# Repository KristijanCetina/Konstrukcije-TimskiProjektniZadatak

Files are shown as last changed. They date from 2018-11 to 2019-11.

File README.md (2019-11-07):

# Konstrukcije - Timski projektni zadatak
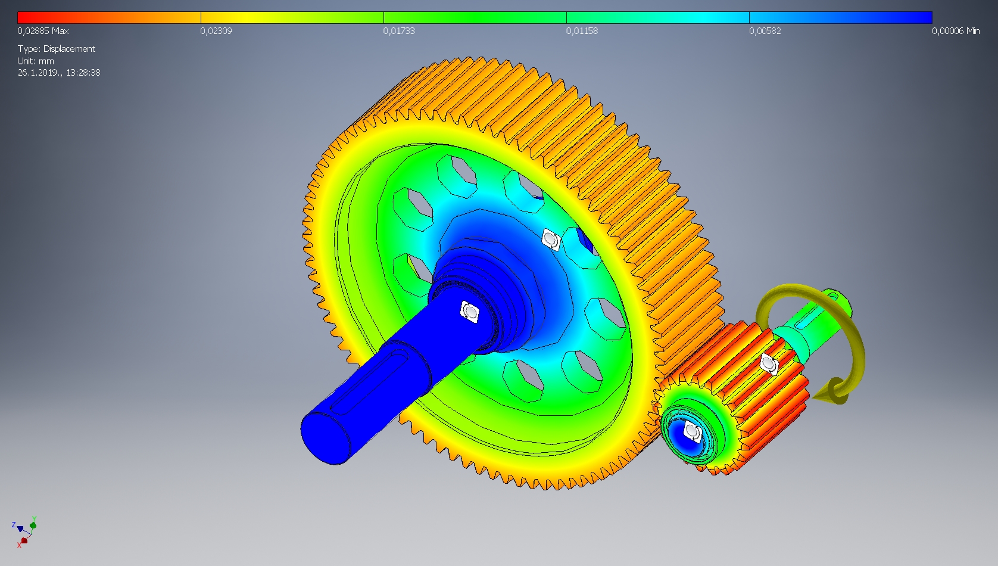
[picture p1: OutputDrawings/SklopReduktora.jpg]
Sklop reduktora Sklop Reduktora

U ovom radu predstavljamo proračun strojnog sklopa - 1-stupanjskog reduktora zajedno s pripradajućim vratilima i ležajevima koji je zadan kao timski projektni zadatak iz kolegija Konstrukcije.

Projektni zadatak se sastoji od proračuna zupčanika, vratila i ležajeva sukladno [zadanim parametrima](https://github.com/KristijanCetina/Konstrukcije-TimskiProjektniZadatak/blob/master/TimskiProjektniZadatak.pdf).

3D model reduktora izrađen je uz pomoć [Autodesk Inventora](https://www.google.com/search?q=Autodesk+Inventor).

Detaljni tok proračuna je izrađen u [LaTeX](https://lmgtfy.com/?q=LaTeX&pp=1&s=g&t=w) te kompajliran u .pdf dokument.  
[PDF verzija proračuna s nacrtom](https://github.com/KristijanCetina/Konstrukcije-TimskiProjektniZadatak/blob/master/Projektni%20zadatak_Cetina-Grgin-Mrkic.pdf)

Sve probleme i greške na koje naiđete slobodno ih prijavite na [Issues tabu](https://github.com/KristijanCetina/Konstrukcije-TimskiProjektniZadatak/issues).

## Uvedena su sljedeća pojednostavljena i zanemareni sljedeći dijelovi proračuna:

* kontrolni proračun
* izbor ulja za podmazivanje
* toplinski proračun
* određivanje stupnja korisnosti

Kod proračuna dimenzija zupčanika zanemareni su sljedeći proračuni:
* nosivost boka zuba
* sigurnost na _pitting_ (površinski zamor)
* nosivost korjena zuba

Kod proračuna vratila izrađena je samo kontrola na plastičnu deformaciju prema normi *DIN 743* te je zanemarena kontrola na zamor materijala.

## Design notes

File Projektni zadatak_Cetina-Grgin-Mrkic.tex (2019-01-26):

\documentclass[11pt,a4paper]{report}
\usepackage[utf8]{inputenc}
\usepackage[croatian]{babel}
\usepackage{amsmath, amsfonts, amssymb}
\usepackage{graphicx}
\usepackage{fancyhdr}
\usepackage{color}
\usepackage {tikz}
\usepackage{pgfplots}
\usetikzlibrary {positioning}
\usepackage{tocloft}
\usepackage[hidelinks]{hyperref}
\usepackage[section]{placeins}
\usepackage[final]{pdfpages}
\bibliographystyle{abbrv}%ieeetr, abbrv
\renewcommand{\cftsecleader}{\cftdotfill{\cftdotsep}}
\addto{\captionscroatian}{\renewcommand{\bibname}{Literatura}}

\usepackage[blocks]{authblk}% The option is for block layout

\newcommand{\kolegij}{}
\newcommand{\naslovRada}{Proračun i konstrukcija 1-stupnjskog reduktora s cilindričnim ravnim zubima \\ {\large Timski projektni zadatak}} 
\newcommand{\mailFriendlynaslovRada}{Konstrukcije - projektni zadatak}

%\author{
%Kristijan Cetina \\{\small JMBAG: 2424011721} \\ {\href{mailto:kcetina@politehnika-pula.hr?subject=\mailFriendlynaslovRada}{{\footnotesize kcetina@politehnika-pula.hr}}} \and 
%Stjepan Grgin \\{\small JMBAG: 0112005802} \\ {\href{mailto:sgrgin@politehnika-pula.hr?subject=\mailFriendlynaslovRada}{{\footnotesize sgrgin@politehnika-pula.hr}}} \and 
%Igor Mrkić \\{\small JMBAG: 0114017089} \\ {\href{mailto:imrkic@politehnika-pula.hr?subject=\mailFriendlynaslovRada}{{\footnotesize imrkic@politehnika-pula.hr}}}
%}

\author[1]{Kristijan Cetina}
\author[2]{Stjepan Grgin}
\author[3]{Igor Mrkić}

\affil[1]{\href{mailto:kcetina@politehnika-pula.hr?subject=\mailFriendlynaslovRada}{kcetina@politehnika-pula.hr} JMBAG: 2424011721}
\affil[2]{\href{mailto:sgrgin@politehnika-pula.hr?subject=\mailFriendlynaslovRada}{sgrgin@politehnika-pula.hr} JMBAG: 0112005802}
\affil[3]{\href{mailto:imrkic@politehnika-pula.hr?subject=\mailFriendlynaslovRada}{imrkic@politehnika-pula.hr} JMBAG: 0114017089}

%\title{\kolegij \\ \naslovRada}
\title{\naslovRada}
\date{Pula, \today}

\begin{document}
\pgfplotsset{width=\textwidth,compat=newest}

\begin{titlepage}
\clearpage
\begin{center}
\begin{Huge}
POLITEHNIKA PULA\\
\end{Huge}
\begin{LARGE}
Visoka tehničko-poslovna škola s p.j.\\
Stručni studij politehnike\\
\end{LARGE}
\end{center}
\vspace{3cm}
{\let\newpage\relax\maketitle}
\thispagestyle{empty}
\vfill
\begin{abstract}

U ovom radu predstavljamo proračun strojnog sklopa 1-stupanjskog reduktora zajedno s pripradajućim vratilima i ležajevima koji je zadan kao sastavni dio kolegija Konstrukcije.

Konstrukcijski sklop izrađen je unutar ograničenja zadanih projektnim zadatkom.
Izrađeni su proračuni dimenzija zopčanika i vratila, proračun momenata i sila na zupčanicima, preliminarni i kontrolni proračun vratila, proračun steznog spoja te valjnih ležajeva.
Na kraju se nalaze radionički nacrti kao i sklopni crtež sklopa.

Elementi proračuna koji su izostavljeni navedeni su u opis zadatka i oganičenja u poglavlju \ref{OpisIOgranicenja}

\vspace{3cm}

\begin{tabbing}
\hspace{50pt}\=\kill
 Kolegij: \> Konstrukcije\\
 Mentori: \> Milenko Jokić, dipl. ing. stroj. \\ 
  \> Feđa Balić, mag. ing. mech.
\end{tabbing} 

\end{abstract}
\end{titlepage}
\includepdf[fitpaper]{TimskiProjektniZadatak.pdf}
\tableofcontents
%\listoftables	%ako ih ima puno prebaci na kraj dokumenta
%\listoffigures	%ako ih ima puno prebaci na kraj dokumenta

%Ovdje kreće rad ili može se koristiti
%\input{filename} (da nastavi pisati kako da je copy/paste) ili
%\include{filename} (da ubaci na novu stranicu. Ok za nova poglavlja i sl)
\chapter{Opis zadatka i ograničenja}\label{OpisIOgranicenja}
\section{Uvod}
Ovaj projektni zadatak nastao je kao obavezni zadatak u sklopu kolegija Konstrukcije koji se održava pod vodstvom Milenka Jokića, dipl.ing., predavača na stručnom studiju politehnike pri Politehnici Pula te asistenciju Feđe Balića, mag. ing. mech.

Prema zadanom predlošku (predložak 3) i zadanim podacima konstriran je 1-stupanjski reduktor s cilindričnim ravnim zubima.
Uvedena su sljedeća pojednostavljena i zanemareni sljedeći dijelovi proračuna:
\begin{itemize}
\item kontrolni proračun
\item izbor ulja za podmazivanje
\item toplinski proračun
\item određivanje stupnja korisnosti
\end{itemize}
Kod proračuna dimenzija zupčanika zanemareni su sljedeći proračuni:
\begin{itemize}
\item nosivost boka zuba
\item sigurnost na \textit{pitting} (površinski zamor)
\item nosivost korjena zuba
\end{itemize}
Kod proračuna vratila izražena je samo kontrola na plastičnu deformaciju te je zanemarena kontrola na zamor materijala.
\newpage
\section{Mehaničke karakteristike materijala}
Zadani materijal za izradu reduktora je Č0745 (E360) čije su karakteristike preuzete iz literature \cite{potrebniMaterijali} te su navedeni u tablici \ref{MehanickeKarakteristikeMaterijala}
\begin{table}[h]
\begin{tabular}{|l|r|}\hline 
Karakteristika & Čvrstoća $\dfrac{N}{mm^2}$ \\ \hline 
Vlačna čvrstoća & $R_m=700 $ \\ \hline 
Granica tečenja & $R_e=370 $ \\ \hline 
Trajna ishodišna dinamička čvrstoča pri vlaku & $R_{d0}=370 $ \\ \hline 
Trajna iizmjenična dinamička čvrstoča pri vlaku/tlaku & $R_{d-1}=320 $ \\ \hline 
Trajna ishodišna dinamička čvrstoča pri savijanju & $R_{ds0}=520 $ \\ \hline 
Trajna izmjenična dinamička čvrstoča pri savijanju & $R_{ds-1}=340 $ \\ \hline 
Trajna ishodišna dinamička čvrstoča pri torziji & $R_{dt0}=260 $ \\ \hline 
Trajna izmjenična dinamička čvrstoča pri torziji & $R_{dt-1}=370 $ \\ \hline 
Granica tečenja pri vlaku/tlaku & $R_{eN}=360 $ \\ \hline 
Granica tečenja pri savijanju & $R_{esN}=430 $ \\ \hline 
Granica tečenja pri torziji & $R_{etN}=250 $ \\ \hline 
\end{tabular} 
Vrijednosti označene s indeksom \emph{N} odnose se na nazivni promjer $d_N=16\,mm$.
\caption{Mehaničke karakteristike korištenog materijala Č0745} \label{MehanickeKarakteristikeMaterijala}
\end{table}

\chapter{Proračun sklopa}
\section{Proračun dimenzija zupčanika}
Na temelju poznatih pogonskih podatak određen je minimalni diobeni promjer pogonskog zupčanika po izrazu
\begin{equation}
d_1\geq 4045 \cdot \sqrt[3]{\frac{P_1}{\psi_b \cdot n_1} \cdot \frac{i_z +1}{i_z}\cdot K_A \cdot 
K_V \cdot K_{H\alpha} \cdot K_{H\beta} \cdot \left(\frac{S_{Hmin}}{\sigma_{Hlim}}\right)^2 }\label{equ:d1minimalno}
\end{equation}
Pri čemu je $\psi_b=1$ - omjer širine zupčanika i diobenog promjera,
$P_1 \, [kW]$ - snaga pogonskog stroja,
$n_1 \, [s^{-1}]$ - broj okretaja pogonskog stroja,
$i_z$ - željeni prijenosni omjer,
$K_A=2$ - faktor primjene očitan iz tablice \cite{potrebniMaterijali},
$K_V=1$ - faktor dodatnih dinamičkih opterećenja,
$K_{H\alpha}=1$ - faktor raspodjele opterećenja na zube koji su istovremeno u zahvatu,
$K_{H\beta}=1$ - faktor raspodjele opterećenja uzduž boka zuba,
$S_{Hmin}=1,3$ - stupanj sigurnosti na površinski zamor (\textit{pitting}),
$\sigma_{H\lim}=1$ - trajna dinamička čvrstoća boka zuba na kontaktna naprezanja.

Uvrštavanje poznatih podataka u \eqref{equ:d1minimalno} dobije se minimalni diobeni promjer pogonskog zupčanika $$d_1\geq 100,3\,mm$$

Broj zuba pogonskog zupčanika određen je u odnosu na njegovu kutnu brzinu po izrazu
\begin{equation}
\nu=\frac{d_1 \cdot n_1 \cdot \pi}{60}\label{equ:kutnaBrzina}
\end{equation}
Uvrštavanje poznatih podataka u \eqref{equ:kutnaBrzina} dobivena je kutna brzina
$$\nu=5,77 ms^{-1}$$
te je iz tablice \cite{potrebniMaterijali} očitan mogući raspon broja zuba te je usvojen 
$$\mathbf{z_1=21}$$
Broj zuba gonjenog zupčanika je određen
\begin{align*}
z_2&=z_1 \cdot i_z\\
z_2&=21 \cdot 4\\
z_2&=\mathbf{84}
\end{align*}
Stvarni i željeni prijenosni omjer su isti $$i_z=\mathbf{i_{stv}=\frac{z_2}{z_1}=4}$$
Normalni modul zuba $m_n$ je izračunat i odabran na osnovu standardnih mjera:
\begin{align*}
m_n&=\frac{d_1}{z_1}\\
m_n&=\frac{100,3}{21}\\
m_n&=4,776 mm \Rightarrow \mathbf{m_n=5\, mm}
\end{align*}
Razmak između osi zupčanika $a$ je određen:
\begin{align*}
a&=\frac{m_n}{2} \cdot (z_1 + z_2)\\
a&=\frac{5}{2} \cdot 105\\
a&=\mathbf{262,5\,mm}
\end{align*}
Stvarni diobeni promjer pogonskog zupčanika izračunat je u odnosu na normalni modul i ranije određen broj zuba
\begin{align*}
d_1&=m_n \cdot z_1\\
d_1&=5 \cdot 21\\
d_1&=\mathbf{105 \, mm}
\end{align*}
Širina gonjenog zupčanika:
\begin{align*}
b_2&=\psi_b \cdot d_1\\
b_2&=1 \cdot 105\\
b_2&=\mathbf{105 \,mm}
\end{align*}
Širina pogonskog zupčanika je uvećana za 5 mm u odnosu na gonjeni zupčanik radi aksijalnih pomaka
\begin{align*}
b_1&=b_2+5\,mm\\
b_1&=\mathbf{110 \,mm}
\end{align*}
Diobeni promjer gonjenog zupčanika:
\begin{align*}
d_2&=m_n \cdot z_2\\
d_2&=5 \cdot 84\\
d_2&=\mathbf{420 \,mm}
\end{align*}
Kao zahvatni kut između zupčanika je odabran standardni kut $\mathbf{\alpha_n=20^\circ}$.
Radijalna zračnost:
\begin{align*}
c&=c^* \cdot m_n\\
c&=0,25 \cdot 5\\
c&= \mathbf{1,25 \, mm}
\end{align*}
Visina korijena zuba:
\begin{align*}
h_f&=m_n+c\\
h_f&=5+1,25\\
h_f&=\mathbf{6,25 \,mm}
\end{align*}
Promjer preko korijena zuba zupčanika:
\begin{align*}
d_{f1}&=d_1-2 \cdot h_f && d_{f2}=d_2-2 \cdot h_f\\
d_{f1}&=105-2 \cdot 6,25 && d_{f2}=420-2 \cdot 6,25\\
d_{f1}&=\mathbf{92,5 \,mm} && d_{f2}=\mathbf{407,5 \,mm}
\end{align*}
Promjer preko glave zuba zupčanika:
\begin{align*}
d_{a1}&=2 \cdot a - d_{f2} - 2 \cdot c  && d_{a2}=2 \cdot a - d_{f1} - 2 \cdot c\\
d_{a1}&=2 \cdot 262,5 - 407,5 - 2 \cdot 1,25 && d_{a2}=2 \cdot 262,5 - 92,5 - 2 \cdot 1,25\\
d_{a1}&=\mathbf{115 \,mm} && d_{a2}=\mathbf{430 \,mm}
\end{align*}

\section{Proračun sila i momenata na zupčanicima}
Moment na ulaznom vratilu:
\begin{align*}
T_1&=\frac{P_1}{\omega_1}=\frac{P_1 \cdot 60}{2 \cdot \pi \cdot n_1}\\
T_1&=\frac{14 \cdot 10^3 \cdot 60}{2 \cdot \pi \cdot 1100}\\
T_1&=\mathbf{121,5 \, Nm}
\end{align*}
Snaga na izlaznom vratilu je umanjena za gubitke u sustavu.
\begin{align*}
P_2&=\prod_{i=1}^{n} \eta_i \cdot P_1\\
P_2&=(0,99 \cdot 0,98 \cdot 0,98) \cdot 14\cdot10^3\\
P_2&=\mathbf{13311 \, W}
\end{align*}
Brzina vrtnje na izlaznom vratilu $n_2=\dfrac{n_1}{i}=\dfrac{1100}{4}=\mathbf{275 \, min^{-1}}$.
Moment na izlaznom vratilu:
\begin{align*}
T_2&=\frac{P_2}{\omega_1}=\frac{P_2 \cdot 60}{2 \cdot \pi \cdot n_2}\\
T_2&=\frac{13311 \cdot 60}{2 \cdot \pi \cdot 275}\\
T_2&=\mathbf{462 \, Nm}
\end{align*}
Obodna sila na zupčanicima:
\begin{align*}
F_{t1}&=\frac{2 \cdot T_1}{d_1} && F_{t2}=\frac{2 \cdot T_2}{d_2}\\
F_{t1}&=\frac{2 \cdot 121,5}{0,105} && F_{t2}=\frac{2 \cdot 462}{0,42}\\
F_{t1}&=\mathbf{2314 \, N} && F_{t2}=\mathbf{2200 \, N}
\end{align*}
Radijalna sila na zupčanicima:
\begin{align*}
F_{r1}&=F_{t1} \cdot \tan \alpha_n && F_{r2}=F_{t2} \cdot \tan \alpha_n \\
F_{r1}&=2314 \cdot \tan 20^{\circ} && F_{r2}=2200 \cdot \tan 20^{\circ} \\
F_{r1}&=\mathbf{842 \, N} && F_{r2}=\mathbf{801 \, N}
\end{align*}
Rezultantna sila na zupčanicima:
\begin{align*}
F_1&=\sqrt{F_{t1}^2+F_{r1}^2} && F_2=\sqrt{F_{t2}^2+F_{r2}^2}\\
F_1&=\sqrt{2314^2+842^2} && F_2=\sqrt{2200^2+801^2}\\
F_1&=\mathbf{2462 \, N} && F_2=\mathbf{2341 \, N}
\end{align*}
S obzirom da su ležajevi jednako udaljeni od središta zupčanika svaki od njih trpi jednaku silu:
\begin{align*}
F_{A1}&=F_{B1}=\frac{F_1}{2} && F_{A2}=F_{B2}=\frac{F_2}{2}\\
F_{A1}&=F_{B1}=\frac{2462}{2} && F_{A2}=F_{B2}=\frac{2341}{2}\\
F_{A1}&=F_{B1}=\mathbf{1231 \, N} && F_{A2}=F_{B2}=\mathbf{1171 \, N}
\end{align*}

\section{Proračun vratila}
\subsection{Preliminarni proračun vratila}
Minimalni potrebni promjer vratila izračunat je pomoću izraza:
\begin{equation}
d\geq \sqrt[3]{\frac{16 \cdot T_n \cdot K_A \cdot S}{\pi \cdot R_{dt0}}}\label{equ_minimalniPromjerVratila}
\end{equation}
Pri čemu je $T_n$ - nazivni okretni moment,
$S$ - faktor sigurnosti u rasponu od 10 do 15 zbog zanemarivanja naprezanja uzrokovanih momentom savijanja kao i nepoznavanja konačnog oblika vratila, koncentracija naprezanja i površinske obrade.
$R_{dt0}$ - trajna ishodišna dinamička čvrstoća materija pri torziji. Očitan iz tablice \cite{krivzan1998osnove}

\subsubsection{Pogonsko vratilo}
Za pogonsko vratilo uvrštavanjem u izraz \eqref{equ_minimalniPromjerVratila} izračunati minimalni promjer je:
\begin{align*}
d&\geq \sqrt[3]{\frac{16 \cdot 121,5 \cdot 10^3 \cdot 2 \cdot 11}{\pi \cdot 260}}\\
d&\geq 37,41 \,mm
\end{align*}

Prema tablici\cite{potrebniMaterijali} standardnih dimenzija krajeva cilindričnog vratila prema normi DIN 748 usvojena je dimenzija $\mathbf{38 \times 80 \,DIN \,748}$ ($\phi38k6$).
Maksimalni radijus prijelaza je $r_{max}=1 mm$.

Prema tablici standardnih dimenzija uložnih pera\cite{potrebniMaterijali} po DIN 6885 normi usvojeno je pero $\mathbf{DIN6885-A 10 \times 8 \times 70-E295}$ s dubinom utora u vratilu $t_1=5mm$ i utorom u glavini $t_2=3,3mm$.

Promjer na poziciji ležaja uzimajući u obzir standardne dimenzije ležajeva $d_L=d+7mm= \mathbf{45 \,mm}$.
Prema katalogu proizvođača ležajeva\cite{skf} odabran je ležaj \textbf{SKF 6008} s potrebnom dimenzijom oslonca ležaja $44,6 \, mm \leq d_a \leq 49,25 \, mm$ te je odabran $\mathbf{d_a=48mm}$.

\subsubsection{Gonjeno vratilo}
Za gonjeno vratilo uvrštavanjem u izraz \eqref{equ_minimalniPromjerVratila} izračunati minimalni promjer je:
\begin{align*}
d&\geq \sqrt[3]{\frac{16 \cdot 462 \cdot 10^3 \cdot 2 \cdot 11}{\pi \cdot 260}}\\
d&\geq 58,39 \,mm
\end{align*}
Prema tablici\cite{potrebniMaterijali} standardnih dimenzija krajeva cilindričnog vratila prema normi DIN 748 usvojena je dimenzija $\mathbf{60 \times 140 \,DIN \, 748}$ ($\phi60m6$).
Maksimalni radijus prijelaza je $r_{max}=1,6 mm$.

Prema tablici standardnih dimenzija uložnih pera\cite{potrebniMaterijali} po DIN 6885 normi usvojeno je pero $\mathbf{DIN6885-A 18 \times 11 \times 125-E295}$ s dubinom utora u vratilu $t_1=7mm$ i utorom u glavini $t_2=4,4mm$.

Promjer na poziciji ležaja $d_L=d+5mm= \mathbf{65 \,mm}$.
Prema katalogu proizvođača ležajeva\cite{skf} odabran je ležaj \textbf{SKF 31913} s potrebnom dimenzijom oslonca ležaja $73 \, mm \leq d_a \leq 86 \, mm$ te je odabran $\mathbf{d_a=84mm}$.

\subsection{Kontrolni proračun vratila}
Na slici \ref{fig:kriticniPresjeci} prikazani su predviđeni kritični presjeci na vratilima reduktora za koje je izvršena provjera na plastičnu deformaciju prema normi DIN 743.
\begin{figure}[!h]
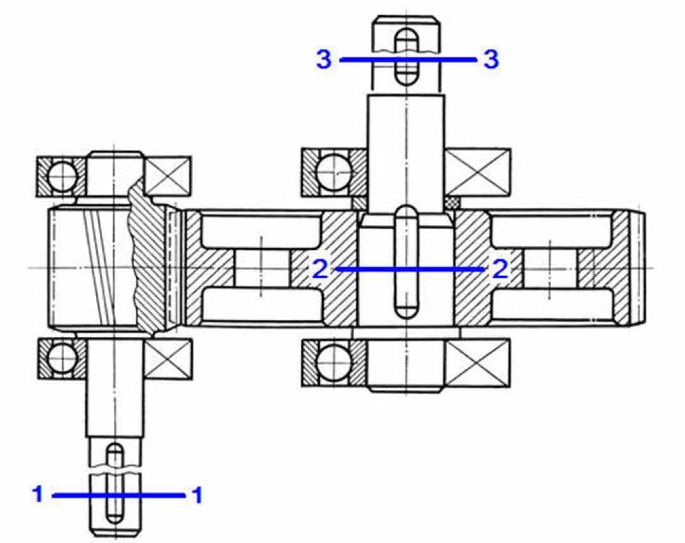
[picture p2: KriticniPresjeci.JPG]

\caption{Kritični presjeci na vratilima reduktora}\label{fig:kriticniPresjeci}
\end{figure}

Na pogonskom vratilu provjera je izvšena u presjeku 1-1 (na spoju reduktora s pogonskim strojem) gdje je vratilo najtanje.
Na gonjenom vratilu reduktora provjera je izvršena na označenim presjecima 2-2 i 3-3.

Kontrolom na plastičnu deformaciju računa se koliko je puta granica tečenja $R_e$ ili $R_{p0,2}$ veća od najvećeg naprezanja.
Naprezanja se javljaju kao posljedica opterećenja $M_{s \, max}$, $F_{a \, max}$ i $T_{max}$.
Kao maksimana opterećenja uzeta su 3 puta veća on normalnih opterećenja koja se mogu javiti kod pokretanja ili zaustavljana stoja ili raznih udarnih opterećenja.
Faktor sigurnosti koji treba biti veći ili jedna 1.2 izračunat je pomoću sljedećeg izraza
\begin{equation}
S_p=\frac{1}{\sqrt{\left( \frac{\sigma_{s \, max}}{R_{es}}+\frac{\sigma_{v,tl \, max}}{R_e}\right)^2+ \left( \frac{\tau_{t \, max}}{R_{et}}\right)^2}}\geq 1,2 \label{equ_faktorSigurnostiPlasticeDeformacije}
\end{equation}
Stvarne granice tečenja su određene uzimajući u obzir tehnološki faktor $K_t$ zbog smanjenja granice tečenja s povećanjem promjera vratila zbog nehomogenosti materijala. Za korišteni materijal E360 (Č0745) korišten je izraz
\begin{equation}
K_t=1-0,26\cdot \log \left( \frac{D}{32} \right) \label{equ:faktorKt}
\end{equation}
Granice tečenja:
\begin{align}
R_e &= K_t \cdot R_{eN} \label{equ:Re} \\
R_{es} &= K_t \cdot R_{esN} \label{equ:Res} \\
R_{et} &= K_t \cdot R_{etN} \label{equ:Ret}
\end{align}
Pri čemu su $R_{eN}$, $R_{esN}$ i $R_{etN}$ su očitani iz tablice \ref{MehanickeKarakteristikeMaterijala}.

\subsubsection{presjek 1-1}
Uvrštavanjem podataka u \eqref{equ:faktorKt} dobiven je tehnološki faktor $K_t$
\begin{align*}
K_t&=1-0,26\cdot \log \left( \frac{D}{32} \right)\\
K_t&=1-0,26\cdot \log \left( \frac{105}{32} \right)\\
K_t&=\mathbf{0,8658}
\end{align*}
U presjeku 1-1 ne javljaju se vlačna niti tlačna opterećenja kao niti poterečenja koje uzrokuju savijenje ili su isti zanemarivo mali već postoji samo moment uvijanja koji uzrokuje torzijsko naprezanje.
Uvršavanjem poznatih podataka u \eqref{equ:Ret} dobivena je stvarna granica plastičnosti materijala pri torziji.
\begin{align*}
R_{et}&=0,8658 \cdot 250\\
R_{et}&=\mathbf{216 \dfrac{N}{mm^2}}
\end{align*}
Maksimalno torzijsko naprezanje koje se javlja u presjeku 1-1:
\begin{align*}
\tau_{t \, max}&=\frac{T_{max}}{W_p}=\frac{3 \cdot T_n \cdot 16}{(d-t_1)^3 \pi}\\
\tau_{t \, max}&=\frac{3 \cdot 121,5\cdot 10^3 \cdot 16}{(35)^3 \pi}\\
\tau_{t \, max}&=\mathbf{43,3 \dfrac{N}{mm^2}}
\end{align*}
Uvršavanjem poznatih podataka u \eqref{equ_faktorSigurnostiPlasticeDeformacije} dobiven je stvarni foktor sigurnosti
\begin{align*}
S_p&=\frac{1}{\sqrt{\left(\frac{43,3}{216}\right)^2}}\\
S_p&=\mathbf{4,99 > 1,2}
\end{align*}
Faktor sigurnosti u presjeku 1-1 zadovoljava postavljeni uvijet.

\subsubsection{presjek 2-2}
Uvrštavanjem podataka u \eqref{equ:faktorKt} dobiven je tehnološki faktor $K_t$
\begin{align*}
K_t&=1-0,26\cdot \log \left( \frac{D}{32} \right)\\
K_t&=1-0,26\cdot \log \left( \frac{80}{32} \right)\\
K_t&=\mathbf{0,8965}
\end{align*}
U presjeku 2-2 ne javljaju se vlačna niti tlačna opterećenja ili su isti zanemarivo mali već postoje samo moment uvijanja koji uzrokuje torzijsko naprezanje i sila na zupčanicima koja uzrokuje savijanje vratila izmeđe oslonaca (ležajeva).
Uvršavanjem poznatih podataka u \eqref{equ:Ret} dobivena je stvarna granica plastičnosti materijala pri torziji.
\begin{align*}
R_{et}&=0,8965 \cdot 250\\
R_{et}&=\mathbf{224 \dfrac{N}{mm^2}}
\end{align*}
Uvršavanjem poznatih podataka u \eqref{equ:Res} dobivena je stvarna granica plastičnosti materijala pri savijanju.
\begin{align*}
R_{es}&=0,8965 \cdot 430\\
R_{es}&=\mathbf{385,5 \dfrac{N}{mm^2}}
\end{align*}

Maksimalno torzijsko naprezanje koje se javlja u presjeku 2-2:
\begin{align*}
\tau_{t \, max}&=\frac{T_{max}}{W_p}=\frac{3 \cdot T_n \cdot 16}{(d-t_1)^3 \pi}\\
\tau_{t \, max}&=\frac{3 \cdot 462\cdot 10^3 \cdot 16}{(71)^3 \pi}\\
\tau_{t \, max}&=\mathbf{19,7 \dfrac{N}{mm^2}}
\end{align*}

Maksimalno naprezanje pri savijanju koje se javlja u presjeku 2-2:
\begin{align*}
\sigma_{s \, max}&=\frac{M_{s \, max}}{W}=\frac{3 \cdot M_s \cdot 32}{(d-t_1)^3 \pi}\\
\sigma_{s \, max}&=\frac{3 \cdot 74358,5  \cdot 16}{(71)^3 \pi}\\
\sigma_{s \, max}&=\mathbf{6,35 \dfrac{N}{mm^2}}
\end{align*}

Uvršavanjem poznatih podataka u \eqref{equ_faktorSigurnostiPlasticeDeformacije} dobiven je stvarni foktor sigurnosti
\begin{align*}
S_p&=\frac{1}{\sqrt{\left( \frac{6,35}{385,5}\right)^2+ \left(\frac{19,7}{224}\right)^2}}\\
S_p&=\mathbf{11,1 > 1,2}
\end{align*}
Faktor sigurnosti u presjeku 2-2 zadovoljava postavljeni uvijet.

\subsubsection{presjek 3-3}
Uvrštavanjem podataka u \eqref{equ:faktorKt} dobiven je tehnološki faktor $K_t$
\begin{align*}
K_t&=1-0,26\cdot \log \left( \frac{D}{32} \right)\\
K_t&=1-0,26\cdot \log \left( \frac{80}{32} \right)\\
K_t&=\mathbf{0,8965}
\end{align*}
U presjeku 3-3 ne javljaju se vlačna niti tlačna opterećenja kao niti poterečenja koje uzrokuju savijenje ili su isti zanemarivo mali već postoji samo moment uvijanja koji uzrokuje torzijsko naprezanje.
Uvršavanjem poznatih podataka u \eqref{equ:Ret} dobivena je stvarna granica plastičnosti materijala pri torziji.
\begin{align*}
R_{et}&=0,8965 \cdot 250\\
R_{et}&=\mathbf{224 \dfrac{N}{mm^2}}
\end{align*}
Maksimalno torzijsko naprezanje koje se javlja u presjeku 3-3:
\begin{align*}
\tau_{t \, max}&=\frac{T_{max}}{W_p}=\frac{3 \cdot T_n \cdot 16}{(d-t_1)^3 \pi}\\
\tau_{t \, max}&=\frac{3 \cdot 462\cdot 10^3 \cdot 16}{(53)^3 \pi}\\
\tau_{t \, max}&=\mathbf{47,4 \dfrac{N}{mm^2}}
\end{align*}
Uvršavanjem poznatih podataka u \eqref{equ_faktorSigurnostiPlasticeDeformacije} dobiven je stvarni foktor sigurnosti
\begin{align*}
S_p&=\frac{1}{\sqrt{\left(\frac{47,4}{224}\right)^2}}\\
S_p&=\mathbf{4,7 > 1,2}
\end{align*}
Faktor sigurnosti u presjeku 3-3 zadovoljava postavljeni uvijet.

\section{Proračun steznog spoja}
Dodirna površina između gonjenog vratila i zupčanika koji se navlači na njega je
\begin{align*}
A_F&=D_F \cdot l_F \cdot \pi \\
A_F&=84 \cdot 100 \cdot \pi \\
A_F&=\mathbf{26389,3 \, mm^2}
\end{align*}
Potrebna sila treba između zupčanika i vratila:
\begin{align*}
F_F&=\frac{2 \cdot T_2 \cdot \nu}{D_F}\\
F_F&=\frac{2 \cdot 462 \cdot 1,8}{84\cdot 10^{-3}}\\
F_F&=\mathbf{19800 \, N}
\end{align*}
Potrebna normalna sila usljed faktora trenja očitanog iz \cite{krivzan1998osnove}(tablica 9.11, str. 346.)
\begin{align*}
F_N&=\frac{F_F}{\mu}\\
F_N&=\frac{19800}{0,11}\\
F_N&=\mathbf{180000 \, N}
\end{align*}
Minimalni potrebni tlak steznog spoja:$$ p_{min}=\frac{F_N}{A_F} = \frac{180000}{26389,3}= \mathbf{6,82 \dfrac{N}{mm^2}}$$
Minimalni potrebni prijeklop je izračunat po izrazu
\begin{equation}
P_{st}=p \cdot D_F \cdot (K_V+K_U)\label{equ:Prijeklop}
\end{equation}
pri kojem su:
\begin{equation}
K_V=\frac{(m_V+1)+(m_V-1) \cdot Q_V^2}{m_V \cdot E_V \cdot (1-Q_V^2)}\label{equ:K_VFaktor}
\end{equation} i
\begin{equation}
K_U=\frac{m_U-1}{m_U \cdot E_U}\label{equ:K_UFaktor}
\end{equation}
gdje je $\nu=0,3$ - \textit{Poissonov} broj za čelik, $E=2,1 \cdot 10^5 \dfrac{N}{mm^2}$ - \textit{Youngov} modul elastičnosti za čelik, $m=\dfrac{1}{\nu}$, $Q_V=\dfrac{D_F}{D_V}$, $D_V\approx 2 \cdot D_F$.
Uvrštavanjem poznatih podataka u \eqref{equ:K_VFaktor} dobiven je faktor 
$$
K_V=\frac{(4,33)+(2,33) \cdot 0,5^2}{3,33 \cdot 2,1\cdot 10^5 \cdot (1-0,5^2)} \mathbf{= 9,36 \cdot 10^{-6} \, \dfrac{mm^2}{N}}
$$
Uvrštavanjem poznatih podataka u \eqref{equ:K_UFaktor} dobiven je faktor
$$
K_U=\frac{m_U-1}{m_U \cdot E_U}=\frac{2,33}{3,33 \cdot 2,1\cdot 10^5}\mathbf{= 3,33 \cdot 10^{-6} \, \dfrac{mm^2}{N}}
$$
Uvrštavanjem dobivenih faktora u \eqref{equ:Prijeklop} dobije se minimalni potrebni prijeklop
$$
P_{st}=6,82 \cdot 84 \cdot (9,36 \cdot 10^{-6} + 3,33 \cdot 10^{-6})= \mathbf{7,27 \, \mu m}
$$
Prilikom navlačenja zupčanika na vratilo pri čvrstom dosjedu dolazi do zaglađivanja hrapavosti površine. Zbog toga je potrebno povećati stvarni minimalni prijeklop po izrazu
\begin{equation}
P_{min}=P_{st}+3,2 \cdot (R_{a \, os}+R_{a \, gl})\label{equ:stvarniMinimalniPrijeklop}
\end{equation}
Pri čemu je $R_a$ - srednje aritmetičko odstupanje profila hrapavosti. Očitan iz \cite{krivzan1998osnove}(tablica 3.44, str 104) za kvalitetu obrade površine N7($R_{a(N7)}=1,6 \, \mu m$).
Uvrštavanjem dobivenih podataka u \eqref{equ:stvarniMinimalniPrijeklop} dobije se stvarni minimalni prijeklop
$$
P_{min}=\mathbf{17,51 \, \mu m}
$$
Maksimalni dopušteni tlak na steznoj površini je određen putem izraza
\begin{equation}
p_{max}\leq\frac{R_e \cdot (1-Q_V^2)}{1,2\cdot \sqrt{3+Q_V^4}}\label{equ:maxTlakSteznePovrsine}
\end{equation}
te uvrštavanjem poznatih podataka u izraz \eqref{equ:maxTlakSteznePovrsine} dobije se
$$
p_{max}\leq\frac{322 \cdot (1-0,5^2)}{1,2\cdot \sqrt{3+0,5^4}}=\mathbf{115 \, \dfrac{N}{mm^2}}
$$
Stvarni dopušteni maksimalni prijeklop po izrazu \eqref{equ:Prijeklop} iznosi
$$
P_{max}=115 \cdot 84 \cdot (9,36 \cdot 10^{-6} + 3,33 \cdot 10^{-6})= \mathbf{122,58 \, \mu m}
$$
Prema \cite{krivzan1998osnove} (str. 77, tablica 3.23) za navedeni stezni spoj odabrana su tolerancijska polja \textbf{H7/r6}.

\section{Proračun valjnih ležajeva}
Trajnost ležajeva se može proračunati po izrazu
\begin{equation}
L_{10h}=\left(\frac{C}{F} \cdot f_t \right)^p \cdot \frac{10^6}{60 \cdot n}
\label{equ:trajnostLezaja}
\end{equation}
pri čemu je $C$ - dinamička nosivost ležaja, $p$ - eksponent vijeka trajanja. Za kuglične ležajeve $p=3$, za ostale $p=\dfrac{10}{3}$ i $f_t$ - temperaturni faktor. Za $\vartheta < 150^\circ C \Rightarrow f_t=1$.

Odabrani ležajevi za pogonsko vratilo imaju dinamičku nosivost $C=17,8 \,kN$.
Uvršavanje poznatih podataka u \eqref{equ:trajnostLezaja} dobije se minimalna trajnost ležaja
\begin{align*}
L_{10h1}&=\left(\frac{17800}{1231} \cdot 1 \right)^3 \cdot \frac{10^6}{60 \cdot 1100}\\
L_{10h1}&=\mathbf{45808\, h}
\end{align*}
Odabrani ležaj zadovoljava potrebnu minimalnu trajnost iz zahtjeva.

Odabrani ležajevi za gonjeno vratilo imaju dinamičku nosivost $C=54,7 \,kN$.
Uvršavanje poznatih podataka u \eqref{equ:trajnostLezaja} dobije se minimalna trajnost ležaja
\begin{align*}
L_{10h2}&=\left(\frac{54700}{1171} \cdot 1 \right)^{\dfrac{10}{3}} \cdot \frac{10^6}{60 \cdot 275}\\
L_{10h2}&=\mathbf{22247650\, h}
\end{align*}
Odabrani ležaj zadovoljava potrebnu minimalnu trajnost iz zahtjeva.

Tehnički podaci odabranog ležaja za pogonsko vratilo se nalazi na slici \ref{fig:lezajPogonskogVratila}.
\begin{figure}

\caption{Tehnički podaci ležaja pogonskog vratila SKF 6008}\label{fig:lezajPogonskogVratila}
\end{figure} 
Tehnički podaci odabranog ležaja za gonjeno vratilo se nalazi na slici \ref{fig:lezajGonjenogVratila}
\begin{figure}[h]

\caption{Tehnički podaci ležaja pogonskog vratila SKF 32913}\label{fig:lezajGonjenogVratila}
\end{figure}

\newpage
\nocite{*}
\addcontentsline{toc}{chapter}{Literatura}
\bibliography{literatura}

\newpage
\appendix
\addcontentsline{toc}{chapter}{Dodatak A: Radionički nacrt pogonskog vratila}
\includepdf[fitpaper]{OutputDrawings/PogonskoVratilo.pdf}
\addcontentsline{toc}{chapter}{Dodatak B: Radionički nacrt gonjenog vratila}
\includepdf[fitpaper]{OutputDrawings/GonjenoVratilo.pdf}
\addcontentsline{toc}{chapter}{Dodatak C: Radionički nacrt gonjenog zupčanika}
\includepdf[fitpaper]{OutputDrawings/GonjeniZupcanikLight.pdf}
\addcontentsline{toc}{chapter}{Dodatak D: Radionički nacrt distantnog prstena}
\includepdf[fitpaper]{OutputDrawings/DistantniPrsten.pdf}
\addcontentsline{toc}{chapter}{Dodatak E: Sklopni nacrt reduktora}
\includepdf[fitpaper]{OutputDrawings/SklopniNacrtReduktora.pdf}
\end{document}

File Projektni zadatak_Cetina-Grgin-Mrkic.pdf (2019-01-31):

# POLITEHNIKA PULA

Visoka tehničko-poslovna škola s p.j.

## Stručni studij politehnike

## Proračun i konstrukcija 1-stupnjskog reduktora s cilindričnim ravnim zubima

Timski projektni zadatak

Kristijan Cetina¹

, Stjepan Grgin²

, and Igor Mrkić³

1kcetina@politehnika-pula.hr JMBAG: 2424011721

2
sgrgin@politehnika-pula.hr JMBAG: 0112005802

3
imrkic@politehnika-pula.hr JMBAG: 0114017089

Pula, 1. veljače 2019.

Sažetak

U ovom radu predstavljamo proračun strojnog sklopa 1-stupanjskog reduktora zajedno s pripradajućim vratilima i ležajevima koji je zadan kao sastavni dio kolegija Konstrukcije.
Konstrukcijski sklop izraden je unutar ograničenja zadanih projektnim zadatkom. Izradeni su proračuni dimenzija zopčanika i vratila, proračun momenata i sila na zupčanicima, preliminarni i kontrolni proračun vratila, proračun steznog spoja te valjnih ležajeva. Na kraju se nalaze radionički nacrti kao i sklopni crtež sklopa.
Elementi proračuna koji su izostavljeni navedeni su u opis zadatka i oganičenja u poglavlju 1

Kolegij: Konstrukcije
Mentori: Milenko Jokić, dipl. ing. stroj.
| Feda Balić, mag. ing. mech.

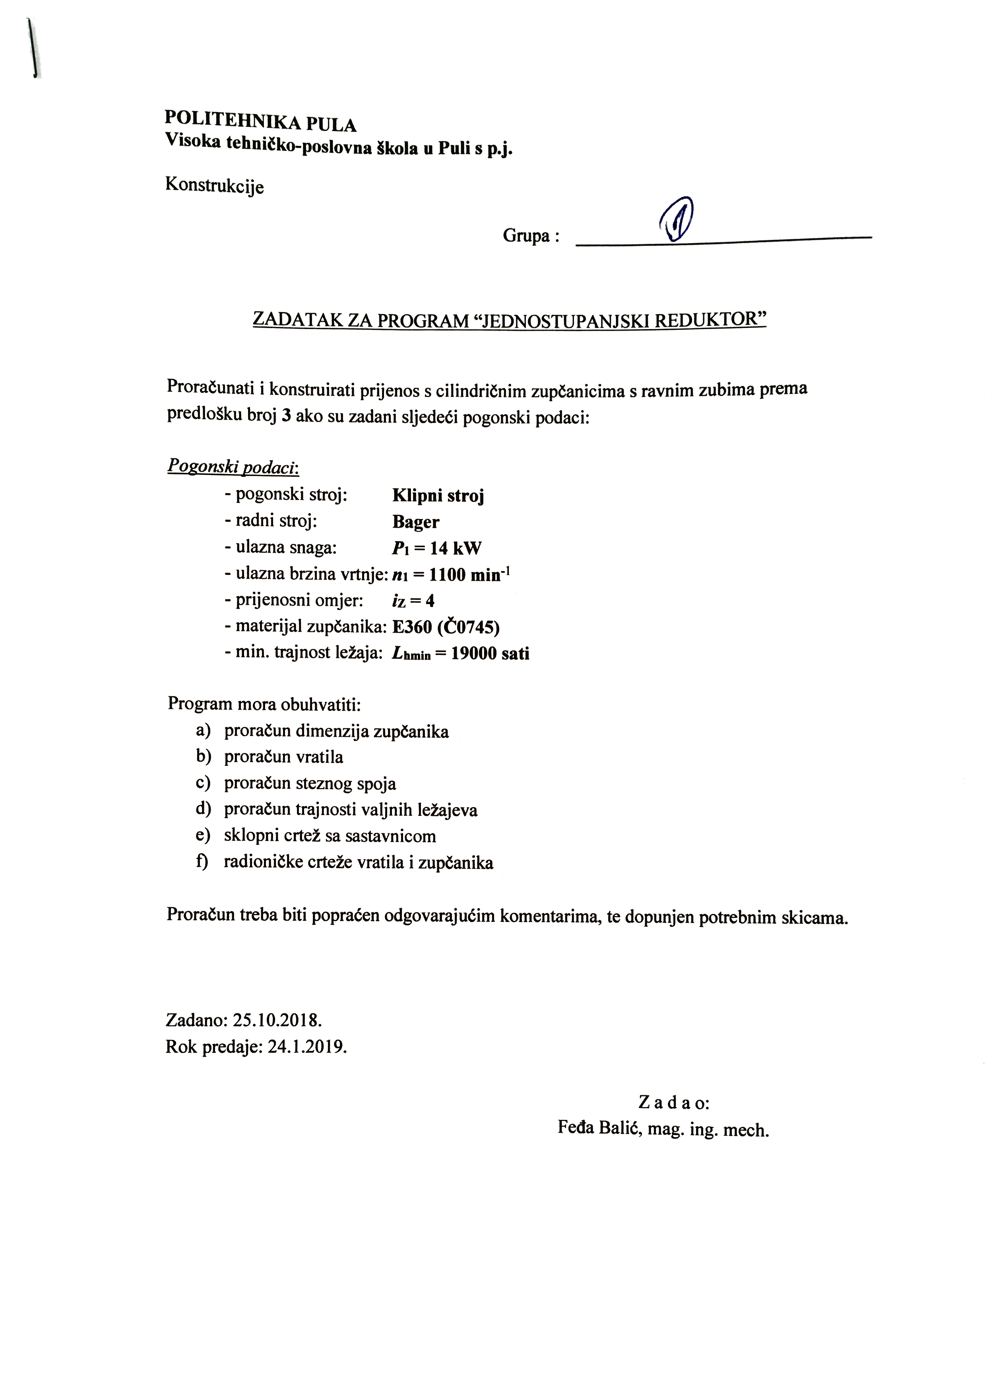
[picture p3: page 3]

# Sadržaj

1 Opis zadatka i ograničenja | 3
2 Proračun sklopa | 5
Literatura | 19
Dodatak A: Radionički nacrt pogonskog vratila | 20
Dodatak B: Radionički nacrt gonjenog vratila | 21
Dodatak C: Radionički nacrt gonjenog zupčanika | 22
Dodatak D: Radionički nacrt distantnog prstena | 23
Dodatak E: Sklopni nacrt reduktora | 24

2

# Poglavlje 1

# Opis zadatka i ograničenja

## 1.1 Uvod

Ovaj projektni zadatak nastao je kao obavezni zadatak u sklopu kolegija Konstrukcije koji se održava pod vodstvom Milenka Jokića, dipl.ing., predavača na stručnom studiju politehnike pri Politehnici Pula te asistenciju Fede Balića, mag. ing. mech.
Prema zadanom predlošku (predložak 3) i zadanim podacima konstriran je 1-stupanjski reduktor s cilindričnim ravnim zubima. Uvedena su sljedeća pojednostavljena i zanemareni sljedeći dijelovi proračuna:
- kontrolni proračun
- izbor ulja za podmazivanje
- toplinski proračun
- odredivanje stupnja korisnosti

Kod proračuna dimenzija zupčanika zanemareni su sljedeći proračuni:

- nosivost boka zuba
- sigurnost na pitting (površinski zamor)
- nosivost korjena zuba

Kod proračuna vratila izražena je samo kontrola na plastičnu deformaciju te je zanemarena kontrola na zamor materijala.

3

## 1.2 Mehaničke karakteristike materijala

Zadani materijal za izradu reduktora je C0745 (E360) čije su karakteristike ˇ preuzete iz literature [1] te su navedeni u tablici 1.1

Karakteristika | N Cvrstoća ˇ mm²
Vlačna čvrstoća | Rm = 700
Granica tečenja | Re = 370
Trajna ishodišna dinamička čvrstoča pri vlaku | Rd0 = 370
Trajna iizmjenična dinamička čvrstoča pri vlaku/tlaku | Rd−1 = 320
Trajna ishodišna dinamička čvrstoča pri savijanju | Rds0 = 520
Trajna izmjenična dinamička čvrstoča pri savijanju | Rds−1 = 340
Trajna ishodišna dinamička čvrstoča pri torziji | Rdt0 = 260
Trajna izmjenična dinamička čvrstoča pri torziji | Rdt−1 = 370
Granica tečenja pri vlaku/tlaku | ReN = 360
Granica tečenja pri savijanju | ResN = 430
Granica tečenja pri torziji | RetN = 250
Vrijednosti označene s indeksom N odnose se na nazivni promjer dN = 16 mm.

Tablica 1.1: Mehaničke karakteristike korištenog materijala C0745 ˇ

4

# Poglavlje 2

# Proračun sklopa

## 2.1 Proračun dimenzija zupčanika

Na temelju poznatih pogonskih podatak odreden je minimalni diobeni promjer pogonskog zupčanika po izrazu

d1 ≥ 4045 ·

3

s
P1

ψb · n1

·

iz + 1
iz
- KA · KV · KHα · KHβ ·
SHmin

σHlim 2
(2.1)

Pri čemu je ψb = 1 - omjer širine zupčanika i diobenog promjera, P1 [kW]
- snaga pogonskog stroja, n1 [s

−1
] - broj okretaja pogonskog stroja, iz -željeni prijenosni omjer, KA = 2 - faktor primjene očitan iz tablice [1], KV = 1 - faktor dodatnih dinamičkih opterećenja, KHα = 1 - faktor raspodjele opterećenja na zube koji su istovremeno u zahvatu, KHβ = 1 - faktor raspodjele opterećenja uzduž boka zuba, SHmin = 1, 3 - stupanj sigurnosti na površinski zamor (pitting), σH lim = 1 - trajna dinamička čvrstoća boka zuba na kontaktna naprezanja.
Uvrštavanje poznatih podataka u (2.1) dobije se minimalni diobeni promjer pogonskog zupčanika

d1 ≥ 100, 3 mm

Broj zuba pogonskog zupčanika odreden je u odnosu na njegovu kutnu brzinu po izrazu

ν =

d1 · n1 · π
60

(2.2)

Uvrštavanje poznatih podataka u (2.2) dobivena je kutna brzina

ν = 5, 77ms⁻¹

te je iz tablice [1] očitan mogući raspon broja zuba te je usvojen

z1 = 21

5

Broj zuba gonjenog zupčanika je odreden

z2 = z1 · iz
z2 = 21 · 4

z2 = 84

Stvarni i željeni prijenosni omjer su isti

iz = istv =

z2
z1

= 4

Normalni modul zuba mn je izračunat i odabran na osnovu standardnih mjera:

mn =

d1
z1

mn =

100, 3
21
mn = 4, 776mm ⇒ mn = 5 mm

Razmak izmedu osi zupčanika a je odreden:

a =

mn
2
- (z1 + z2)

a =

5
2
- 105

a = 262, 5 mm

Stvarni diobeni promjer pogonskog zupčanika izračunat je u odnosu na normalni modul i ranije odreden broj zuba

d1 = mn · z1
d1 = 5 · 21

d1 = 105 mm

Sirina gonjenog zupčanika: ˇ

b2 = ψb · d1
b2 = 1 · 105

b2 = 105 mm

Sirina pogonskog zupčanika je uvećana za 5 mm u odnosu na gonjeni zupčanik ˇ radi aksijalnih pomaka

b1 = b2 + 5 mm
b1 = 110 mm

6

Diobeni promjer gonjenog zupčanika:

d2 = mn · z2
d2 = 5 · 84

d2 = 420 mm

Kao zahvatni kut izmedu zupčanika je odabran standardni kut αn = 20◦ .
Radijalna zračnost:

c = c

∗
- mn
c = 0, 25 · 5

c = 1, 25 mm

Visina korijena zuba:

hf = mn + c
hf = 5 + 1, 25
hf = 6, 25 mm

Promjer preko korijena zuba zupčanika:

df1 = d1 − 2 · hf | df2 = d2 − 2 · hf
df1 = 105 − 2 · 6, 25 | df2 = 420 − 2 · 6, 25
df1 = 92, 5 mm | df2 = 407, 5 mm

Promjer preko glave zuba zupčanika:

da1 = 2 · a − df2 − 2 · c | da2 = 2 · a − df1 − 2 · c
da1 = 2 · 262, 5 − 407, 5 − 2 · 1, 25 | da2 = 2 · 262, 5 − 92, 5 − 2 · 1, 25
da1 = 115 mm | da2 = 430 mm

## 2.2 Proračun sila i momenata na zupčanicima

Moment na ulaznom vratilu:

T1 =

P1
ω1

=

| P1 · 60 2 · π · n1

T1 =

14 · 10³
| · 60
2 · π · 1100
T1 = 121, 5 Nm

Snaga na izlaznom vratilu je umanjena za gubitke u sustavu.

P2 =

Yn

i=1

ηi

- P1

P2 = (0, 99 · 0, 98 · 0, 98) · 14 · 10³

P2 = 13311W

7

Brzina vrtnje na izlaznom vratilu n2 =

n1
i

=

1100
4

= 275 min⁻¹
. Moment
na izlaznom vratilu:

T2 =

P2
ω1

=

P2 · 60
2 · π · n2

T2 =

13311 · 60
2 · π · 275
T2 = 462 Nm

Obodna sila na zupčanicima:

Ft1 =

2 · T1
d1

Ft2 =

2 · T2
d2

Ft1 =

2 · 121, 5
0, 105

Ft2 =

2 · 462
0, 42
Ft1 = 2314 N | Ft2 = 2200 N

Radijalna sila na zupčanicima:

Fr1 = Ft1 · tan αn | Fr2 = Ft2 · tan αn
Fr1 = 2314 · tan 20◦ | Fr2 = 2200 · tan 20◦
Fr1 = 842 N | Fr2 = 801 N

Rezultantna sila na zupčanicima:

F1 =

q
F

2
t1 + F

2
r1 | F2 =

q
| F
| 2
| t2 + F
| 2
| r2
F1 =

p
2314² + 842² | F2 =

p
| 2200² + 801²
F1 = 2462 N | F2 = 2341 N

S obzirom da su ležajevi jednako udaljeni od središta zupčanika svaki od njih trpi jednaku silu:

FA1 = FB1 =

F1

2 | FA2 = FB2 = F2
| 2

FA1 = FB1 =

2462
2 | FA2 = FB2 =
| 2341
| 2
FA1 = FB1 = 1231 N | FA2 = FB2 = 1171 N

## 2.3 Proračun vratila

### 2.3.1 Preliminarni proračun vratila

Minimalni potrebni promjer vratila izračunat je pomoću izraza:

d ≥

3

r
16 · Tn · KA · S

π · Rdt0

(2.3)

8

Pri čemu je Tn - nazivni okretni moment, S - faktor sigurnosti u rasponu od 10 do 15 zbog zanemarivanja naprezanja uzrokovanih momentom savijanja kao i nepoznavanja konačnog oblika vratila, koncentracija naprezanja i površinske obrade. Rdt0 - trajna ishodišna dinamička čvrstoća materija pri torziji. Očitan iz tablice [3]

Pogonsko vratilo

Za pogonsko vratilo uvrštavanjem u izraz (2.3) izračunati minimalni promjer je:

d ≥

3

r
16 · 121, 5 · 10³ · 2 · 11 π · 260
d ≥ 37, 41 mm

Prema tablici[1] standardnih dimenzija krajeva cilindričnog vratila prema normi DIN 748 usvojena je dimenzija 38 × 80 DIN 748 (φ38k6). Maksimalni radijus prijelaza je rmax = 1mm.
Prema tablici standardnih dimenzija uložnih pera[1] po DIN 6885 normi usvojeno je pero DIN6885 − A10 × 8 × 70 − E295 s dubinom utora u vratilu t1 = 5mm i utorom u glavini t2 = 3, 3mm.
Promjer na poziciji ležaja uzimajući u obzir standardne dimenzije ležajeva dL = d + 7mm = 45 mm. Prema katalogu proizvodača ležajeva[4] odabran je ležaj SKF 6008 s potrebnom dimenzijom oslonca ležaja 44, 6 mm ≤ da ≤ 49, 25 mm te je odabran da = 48mm.

Gonjeno vratilo

Za gonjeno vratilo uvrštavanjem u izraz (2.3) izračunati minimalni promjer je:

d ≥

3

r
16 · 462 · 10³ · 2 · 11
π · 260
d ≥ 58, 39 mm

Prema tablici[1] standardnih dimenzija krajeva cilindričnog vratila prema normi DIN 748 usvojena je dimenzija 60 × 140 DIN 748 (φ60m6). Maksimalni radijus prijelaza je rmax = 1, 6mm.
Prema tablici standardnih dimenzija uložnih pera[1] po DIN 6885 normi usvojeno je pero DIN6885 − A18 × 11 × 125 − E295 s dubinom utora u vratilu t1 = 7mm i utorom u glavini t2 = 4, 4mm.
Promjer na poziciji ležaja dL = d + 5mm = 65 mm. Prema katalogu proizvodača ležajeva[4] odabran je ležaj SKF 31913 s potrebnom dimenzijom oslonca ležaja 73 mm ≤ da ≤ 86 mm te je odabran da = 84mm.

9

### 2.3.2 Kontrolni proračun vratila

Na slici 2.1 prikazani su predvideni kritični presjeci na vratilima reduktora za koje je izvršena provjera na plastičnu deformaciju prema normi DIN 743.


Slika 2.1: Kritični presjeci na vratilima reduktora

Na pogonskom vratilu provjera je izvšena u presjeku 1-1 (na spoju reduktora s pogonskim strojem) gdje je vratilo najtanje. Na gonjenom vratilu reduktora provjera je izvršena na označenim presjecima 2-2 i 3-3. Kontrolom na plastičnu deformaciju računa se koliko je puta granica tečenja Re ili Rp0,2 veća od najvećeg naprezanja. Naprezanja se javljaju kao posljedica opterećenja Ms max, Fa max i Tmax. Kao maksimana opterećenja uzeta su 3 puta veća on normalnih opterećenja koja se mogu javiti kod pokretanja ili zaustavljana stoja ili raznih udarnih opterećenja. Faktor sigurnosti koji treba biti veći ili jedna 1.2 izračunat je pomoću sljedećeg izraza

Sp =

1
r
σs max
Res

+

σv,tl max
Re

2
+
τt max
Ret | 2
≥ 1, 2 | (2.4)

Stvarne granice tečenja su odredene uzimajući u obzir tehnološki faktor Kt

10 zbog smanjenja granice tečenja s povećanjem promjera vratila zbog nehomogenosti materijala. Za korišteni materijal E360 (C0745) korišten je izraz ˇ

Kt = 1 − 0, 26 · log
D

32
(2.5)

Granice tečenja:

Re = Kt

- ReN | (2.6)

Res = Kt

- ResN | (2.7)

Ret = Kt

- RetN | (2.8)

Pri čemu su ReN , ResN i RetN su očitani iz tablice 1.1.

presjek 1-1

Uvrštavanjem podataka u (2.5) dobiven je tehnološki faktor Kt

Kt = 1 − 0, 26 · log
D

32

Kt = 1 − 0, 26 · log
105

32

Kt = 0, 8658

U presjeku 1-1 ne javljaju se vlačna niti tlačna opterećenja kao niti poterečenja koje uzrokuju savijenje ili su isti zanemarivo mali već postoji samo moment uvijanja koji uzrokuje torzijsko naprezanje. Uvršavanjem poznatih podataka u (2.8) dobivena je stvarna granica plastičnosti materijala pri torziji.

Ret = 0, 8658 · 250

Ret = 216

N
mm²
Maksimalno torzijsko naprezanje koje se javlja u presjeku 1-1:

τt max =

Tmax
Wp

=

3 · Tn · 16
(d − t1)

3π

τt max =

3 · 121, 5 · 10³
- 16
(35)³π

τt max = 43, 3

N
mm²
Uvršavanjem poznatih podataka u (2.4) dobiven je stvarni foktor sigurnosti

Sp =

1
r
43,3

216 2

Sp = 4, 99 > 1, 2

Faktor sigurnosti u presjeku 1-1 zadovoljava postavljeni uvijet.

11

presjek 2-2

Uvrštavanjem podataka u (2.5) dobiven je tehnološki faktor Kt

Kt = 1 − 0, 26 · log
D

32

Kt = 1 − 0, 26 · log
80

32

Kt = 0, 8965

U presjeku 2-2 ne javljaju se vlačna niti tlačna opterećenja ili su isti zanemarivo mali već postoje samo moment uvijanja koji uzrokuje torzijsko naprezanje i sila na zupčanicima koja uzrokuje savijanje vratila izmede oslonaca (ležajeva). Uvršavanjem poznatih podataka u (2.8) dobivena je stvarna granica plastičnosti materijala pri torziji.

Ret = 0, 8965 · 250

Ret = 224

N
mm²

Uvršavanjem poznatih podataka u (2.7) dobivena je stvarna granica plastičnosti materijala pri savijanju.

Res = 0, 8965 · 430

Res = 385, 5

N
mm²

Maksimalno torzijsko naprezanje koje se javlja u presjeku 2-2:

τt max =

Tmax
Wp

=

3 · Tn · 16
(d − t1)

3π

τt max =

3 · 462 · 10³
- 16
(71)³π

τt max = 19, 7

N
mm²

Maksimalno naprezanje pri savijanju koje se javlja u presjeku 2-2:

σs max =

Ms max
W

=

3 · Ms · 32
(d − t1)

3π

σs max =

3 · 74358, 5 · 16
(71)³π

σs max = 6, 35

N
mm²

12

Uvršavanjem poznatih podataka u (2.4) dobiven je stvarni foktor sigurnosti

Sp =

1
r
6,35
385,5

2
+
19,7

224 2

Sp = 11, 1 > 1, 2

Faktor sigurnosti u presjeku 2-2 zadovoljava postavljeni uvijet.

presjek 3-3

Uvrštavanjem podataka u (2.5) dobiven je tehnološki faktor Kt

Kt = 1 − 0, 26 · log
D

32

Kt = 1 − 0, 26 · log
80

32

Kt = 0, 8965

U presjeku 3-3 ne javljaju se vlačna niti tlačna opterećenja kao niti poterečenja koje uzrokuju savijenje ili su isti zanemarivo mali već postoji samo moment uvijanja koji uzrokuje torzijsko naprezanje. Uvršavanjem poznatih podataka u (2.8) dobivena je stvarna granica plastičnosti materijala pri torziji.

Ret = 0, 8965 · 250

Ret = 224

N
mm²

Maksimalno torzijsko naprezanje koje se javlja u presjeku 3-3:

τt max =

Tmax
Wp

=

3 · Tn · 16
(d − t1)

3π

τt max =

3 · 462 · 10³
- 16
(53)³π

τt max = 47, 4

N
mm²

Uvršavanjem poznatih podataka u (2.4) dobiven je stvarni foktor sigurnosti

Sp =

1
r
47,4

224 2

Sp = 4, 7 > 1, 2

Faktor sigurnosti u presjeku 3-3 zadovoljava postavljeni uvijet.

13

## 2.4 Proračun steznog spoja

Dodirna površina izmedu gonjenog vratila i zupčanika koji se navlači na njega je

AF = DF · lF · π
AF = 84 · 100 · π
AF = 26389, 3 mm²

Potrebna sila treba izmedu zupčanika i vratila:

FF =

2 · T2 · ν
DF

FF =

2 · 462 · 1, 8
84 · 10⁻³
FF = 19800 N

Potrebna normalna sila usljed faktora trenja očitanog iz [3](tablica 9.11, str. 346.)

FN =

FF
µ

FN =

19800
0, 11
FN = 180000 N

Minimalni potrebni tlak steznog spoja:

pmin =

FN
AF

=

180000
26389, 3

= 6, 82

N
mm²

Minimalni potrebni prijeklop je izračunat po izrazu

Pst = p · DF · (KV + KU ) | (2.9)

pri kojem su:

KV =

(mV + 1) + (mV − 1) · Q²
V
mV · EV · (1 − Q²
V

)

| (2.10)

i
KU =
mU − 1 mU · EU | (2.11)

gdje je ν = 0, 3 - Poissonov broj za čelik, E = 2, 1 · 10⁵ N mm²

- Youngov

modul elastičnosti za čelik, m =

1
ν

, QV =

DF
DV

, DV ≈ 2 · DF . Uvrštavanjem

poznatih podataka u (2.10) dobiven je faktor

KV =

(4, 33) + (2, 33) · 0, 5

2
3, 33 · 2, 1 · 10⁵ · (1 − 0, 5

2)

= 9, 36 · 10⁻⁶ mm²

N

14

Uvrštavanjem poznatih podataka u (2.11) dobiven je faktor

KU =

mU − 1
mU · EU

=

2, 33
3, 33 · 2, 1 · 10⁵

= 3, 33 · 10⁻⁶ mm²

N

Uvrštavanjem dobivenih faktora u (2.9) dobije se minimalni potrebni prijeklop
Pst = 6, 82 · 84 · (9, 36 · 10⁻⁶ + 3, 33 · 10⁻⁶ ) = 7, 27 µm

Prilikom navlačenja zupčanika na vratilo pri čvrstom dosjedu dolazi do zagladivanja hrapavosti površine. Zbog toga je potrebno povećati stvarni minimalni prijeklop po izrazu

Pmin = Pst + 3, 2 · (Ra os + Ra gl) | (2.12)

Pri čemu je Ra - srednje aritmetičko odstupanje profila hrapavosti. Očitan iz [3](tablica 3.44, str 104) za kvalitetu obrade površine N7(Ra(N7) = 1, 6 µm). Uvrštavanjem dobivenih podataka u (2.12) dobije se stvarni minimalni prijeklop
Pmin = 17, 51 µm

Maksimalni dopušteni tlak na steznoj površini je odreden putem izraza

pmax ≤

Re · (1 − Q²
V

)

1, 2 ·

q
3 + Q⁴
V

(2.13)

te uvrštavanjem poznatih podataka u izraz (2.13) dobije se

pmax ≤

322 · (1 − 0, 5

2
)

1, 2 ·

p
3 + 0, 5

4

= 115

N
mm²

Stvarni dopušteni maksimalni prijeklop po izrazu (2.9) iznosi

Pmax = 115 · 84 · (9, 36 · 10⁻⁶ + 3, 33 · 10⁻⁶ ) = 122, 58 µm

Prema [3] (str. 77, tablica 3.23) za navedeni stezni spoj odabrana su tolerancijska polja H7/r6.

## 2.5 Proračun valjnih ležajeva

Trajnost ležajeva se može proračunati po izrazu

L10h =

C
F
- ft

p
·

10⁶
60 · n

(2.14)

pri čemu je C - dinamička nosivost ležaja, p - eksponent vijeka trajanja. Za

kuglične ležajeve p = 3, za ostale p =

10
3

i ft - temperaturni faktor. Za ϑ < 150◦C ⇒ ft = 1.

15

Odabrani ležajevi za pogonsko vratilo imaju dinamičku nosivost C = 17, 8 kN. Uvršavanje poznatih podataka u (2.14) dobije se minimalna trajnost ležaja

L10h1 =

17800
1231
- 1

3
·

10⁶
60 · 1100

L10h1 = 45808 h

Odabrani ležaj zadovoljava potrebnu minimalnu trajnost iz zahtjeva. Odabrani ležajevi za gonjeno vratilo imaju dinamičku nosivost C = 54, 7 kN. Uvršavanje poznatih podataka u (2.14) dobije se minimalna trajnost ležaja

L10h2 =

54700
1171
- 1

10
3
·

10⁶
60 · 275

L10h2 = 22247650 h

Odabrani ležaj zadovoljava potrebnu minimalnu trajnost iz zahtjeva. Tehnički podaci odabranog ležaja za pogonsko vratilo se nalazi na slici
2.2. Tehnički podaci odabranog ležaja za gonjeno vratilo se nalazi na slici 2.3

16

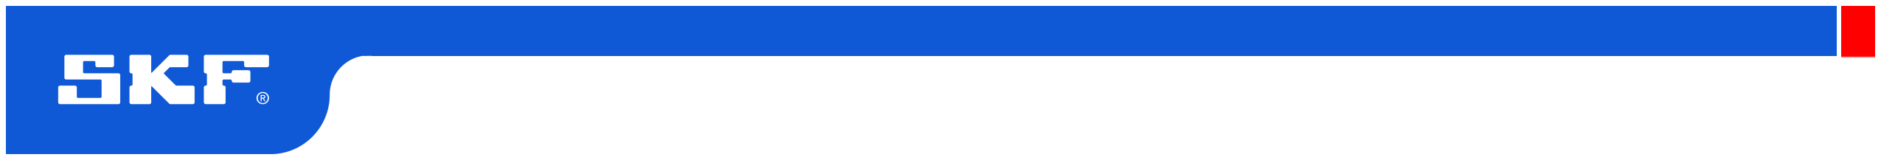
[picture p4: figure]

►
6008

Popular item
SKF Explorer

d a

min. | 44.6 | mm

D

a | max. 63.4 | mm

r

a | max. 1 | mm
d | | 40 | mm
D | | 68 | mm
B | | 15 | mm
d 1 | ≈ | 49.25 | mm
D 2 | ≈ | 61.1 | mm

Dimensions

Abutment dimensions

Calculation data

Basic dynamic load rating | C | 17.8 | kN
Basic static load rating | C 0 | 11 | kN
Fatigue load limit | P u | 0.49 | kN
Reference speed | | 22000 | r/min
Limiting speed | | 14000 | r/min
Calculation factor | k
| r | 0.025
Calculation factor | f 0 | 15

Mass

Mass bearing | 0.19 | kg

Slika 2.2: Tehnički podaci ležaja pogonskog vratila SKF 6008 17

32913

SKF Explorer

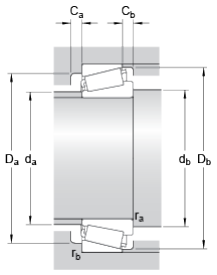
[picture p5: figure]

d a | max. 71 | mm
d b | min. | 73 | mm
D a | min. | 83 | mm

D

a | max. 83 | mm
D b | min. | 86 | mm
C a | min. | 3 | mm
C b | min. | 3 | mm

r

a | max. 1 | mm
r b | max. 1 | mm
d | | 65 | mm
D | | 90 | mm
T | | 17 | mm
d 1 | ≈ | 78.8 | mm
B | | 17 | mm
C | | 14 | mm
r 1,2 | min. 1 | mm
r 3,4 | min. 1 | mm
a | | 16.537 | mm
Dimension series | 2BC

Dimensions

Abutment dimensions

Calculation data

Basic dynamic load rating | C | 54.7 | kN
Basic static load rating | C 0 | 80 | kN
Fatigue load limit | P u | 8.15 | kN
Reference speed | | 5600 | r/min
Limiting speed | | 6700 | r/min
Calculation factor | e | 0.35
Calculation factor | Y | 1.7

Slika 2.3: Tehnički podaci ležaja pogonskog vratila SKF 32913 18

# Literatura

[1] M. Jokić. Zbirka potrebnih materijala i tablica za izradu timskog projektnog zadatka. Politehnika Pula, 2018.
[2] B. Križan. Interna skripta iz kolegija Elementi strojeva 2 za konstrukcijske vježbe. Politehnika Pula, 2018.
[3] B. Križan. Osnove proračuna i oblikovanja konstrukcijskih elemenata. Skolska knjiga, Zagreb, 2008. ˇ
[4] SKF. | Product catalogue. | http://www.skf.com/group/products/
index.html (http://www.skf.com/group/products/index.html) (27.10.2018), 2018.

19

1

2

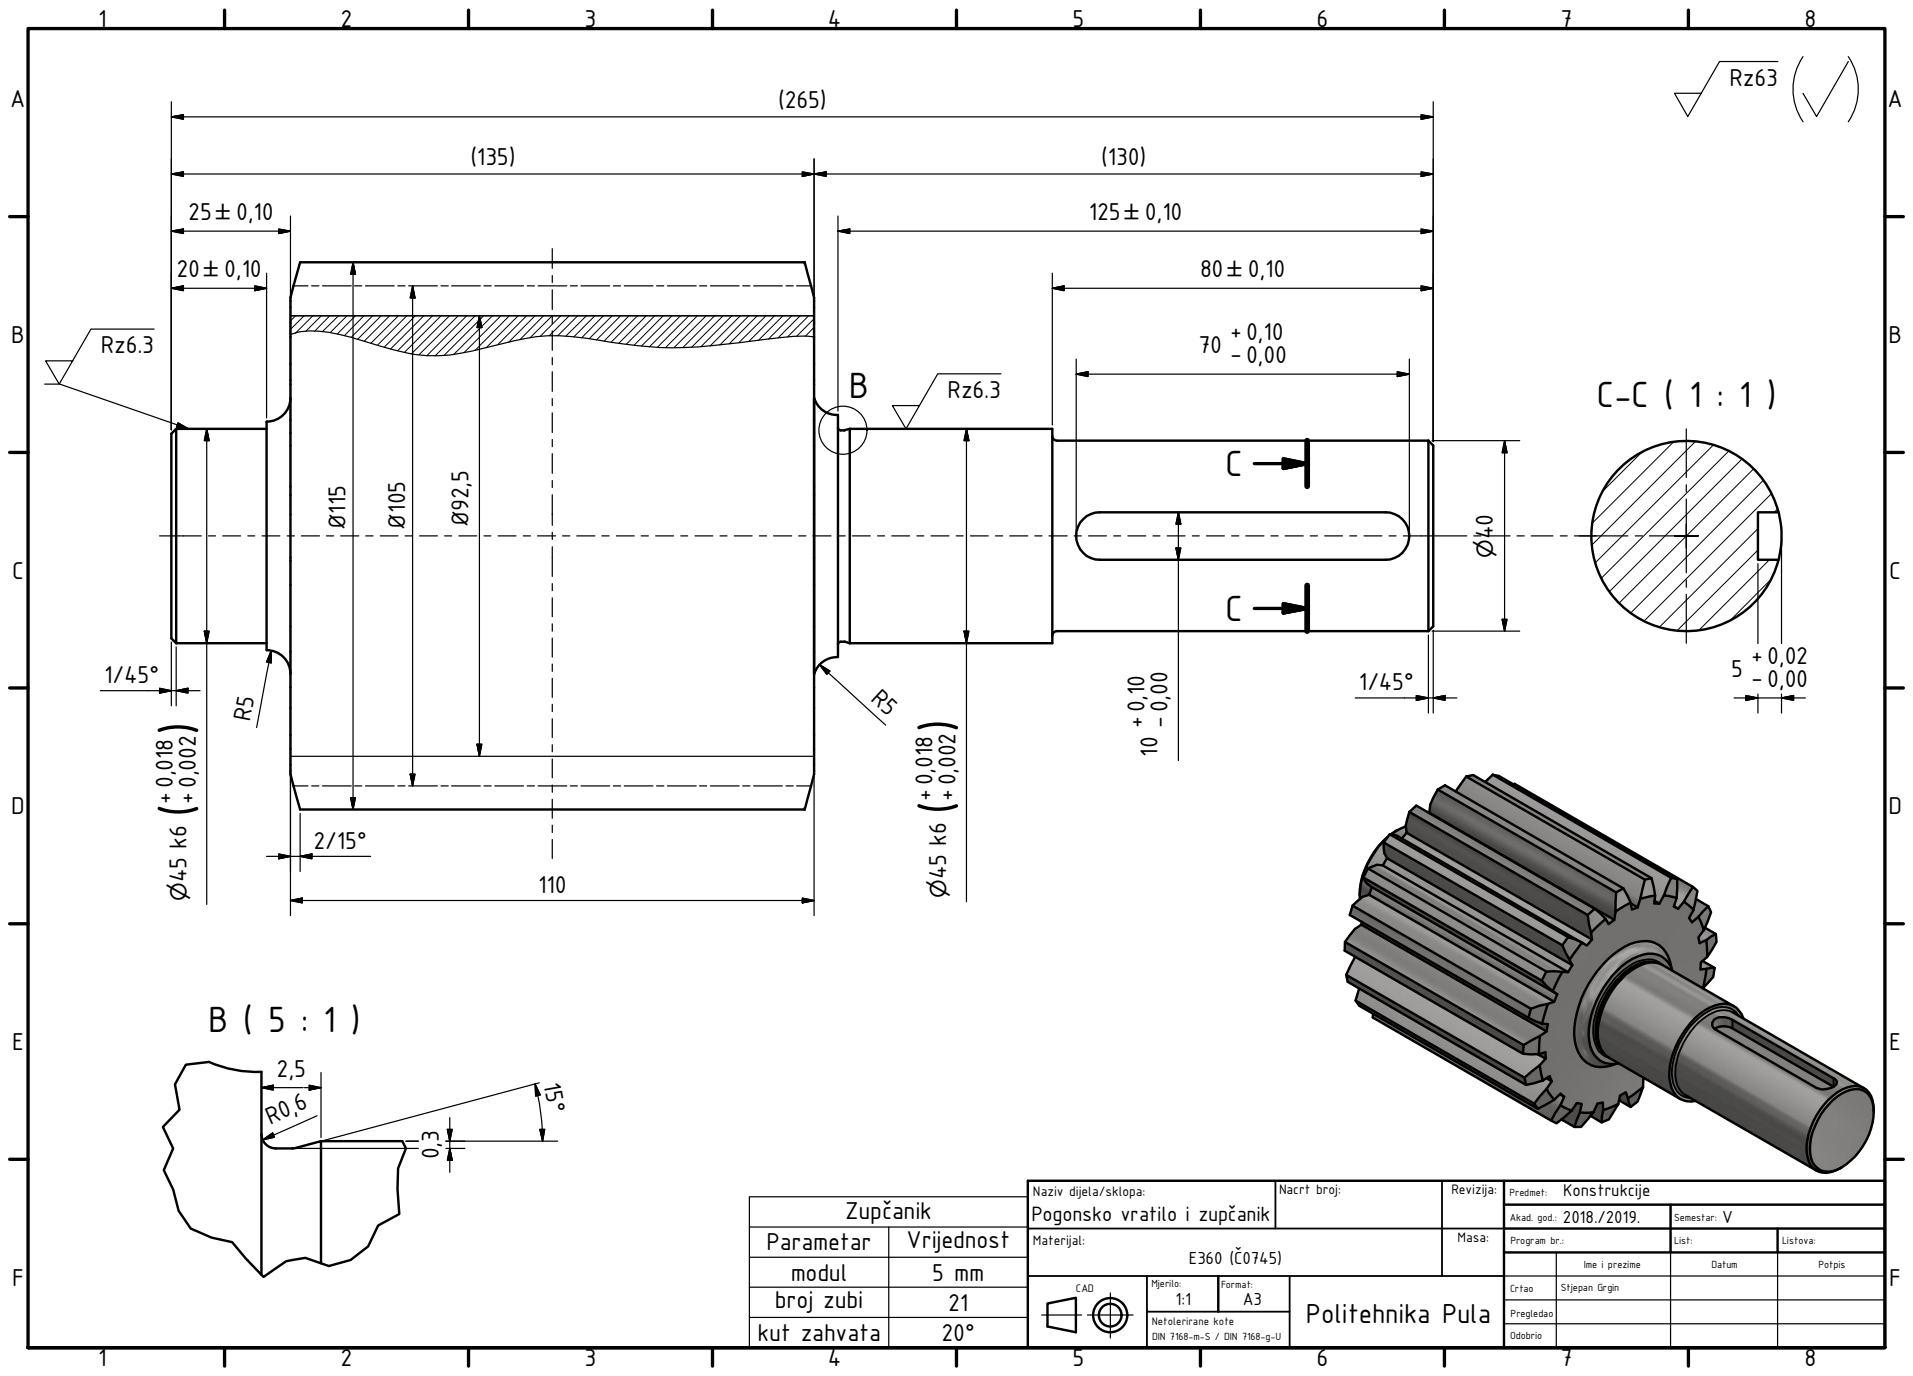
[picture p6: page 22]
F CAD; Netolerirane kote; DIN 7168-m-S / DIN 7168-g-U; Zupúanik; Parametar; Vrijednost; modul; broj zubi; kut zahvata

Naziv dijela/sklopa: Pogonsko vratilo i zupúanik | Nacrt broj: | Revizija: | Konstrukcije Predmet:

2018./2019. Akad. god.: | V Semestar:

Materijal: E360 (ù0745) | Masa: | Program br.: | List: | Listova:

Ime i prezime | Datum | Potpis

Mjerilo: 1:1 | Format: A3 | Politehnika Pula | Crtao | Stjepan Grgin

Pregledao

Odobrio

1

2

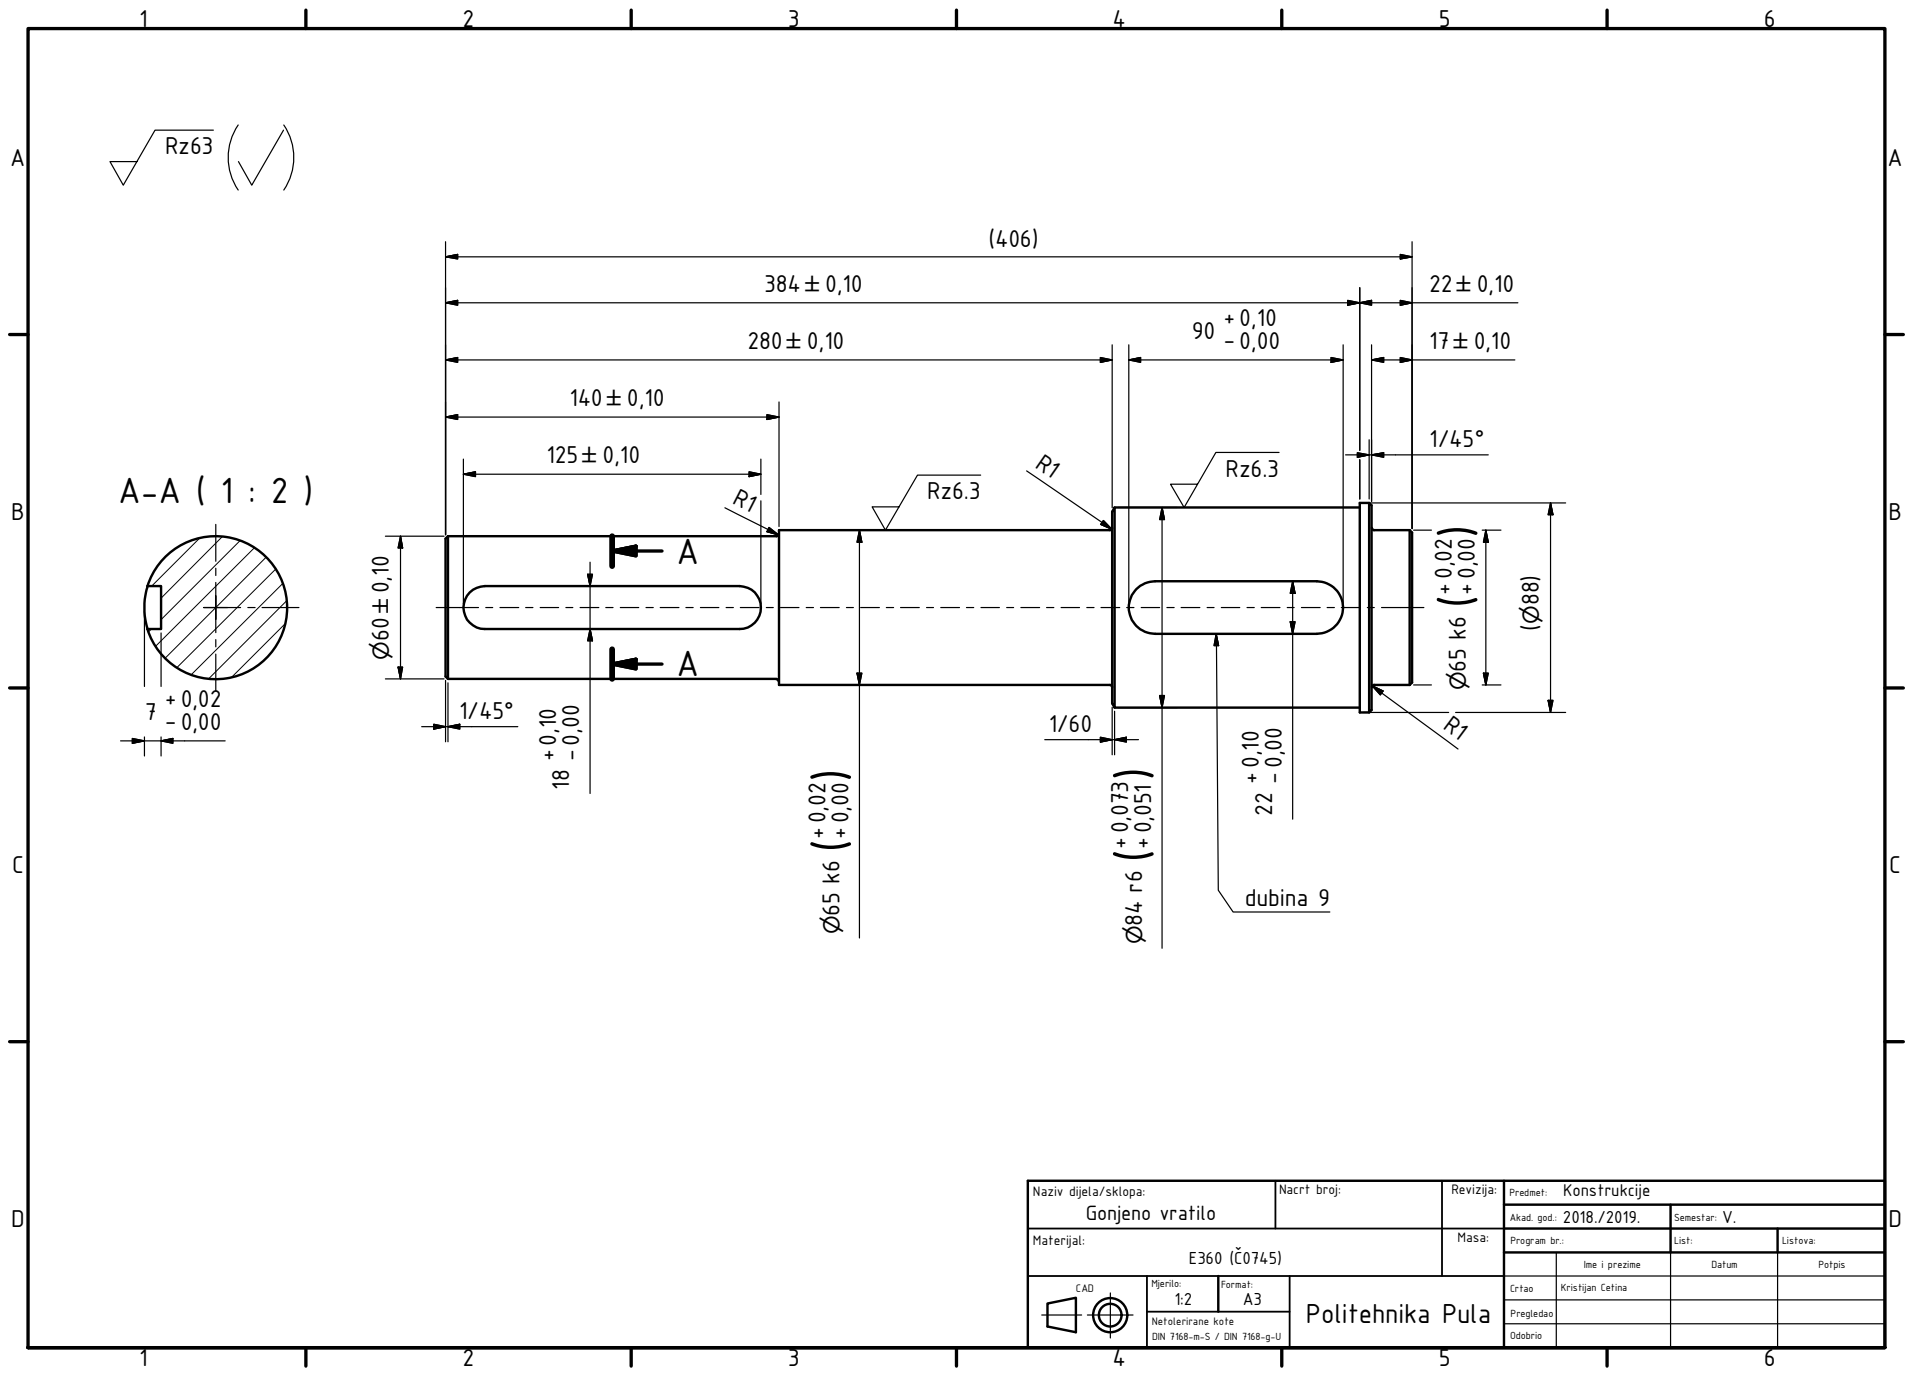
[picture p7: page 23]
Netolerirane kote; DIN 7168-m-S / DIN 7168-g-U; dubina 9

Naziv dijela/sklopa: Gonjeno vratilo | Nacrt broj: | Revizija: | Konstrukcije Predmet:

2018./2019. Akad. god.: | V. Semestar:

Materijal: E360 (ù0745) | Masa: | Program br.: | List: | Listova:

Ime i prezime | Datum | Potpis

CAD | Mjerilo: 1:2 | Format: A3 | Politehnika Pula | Crtao | Kristijan Cetina

Pregledao

Odobrio

A | A-A ( 1 : 2 )

1

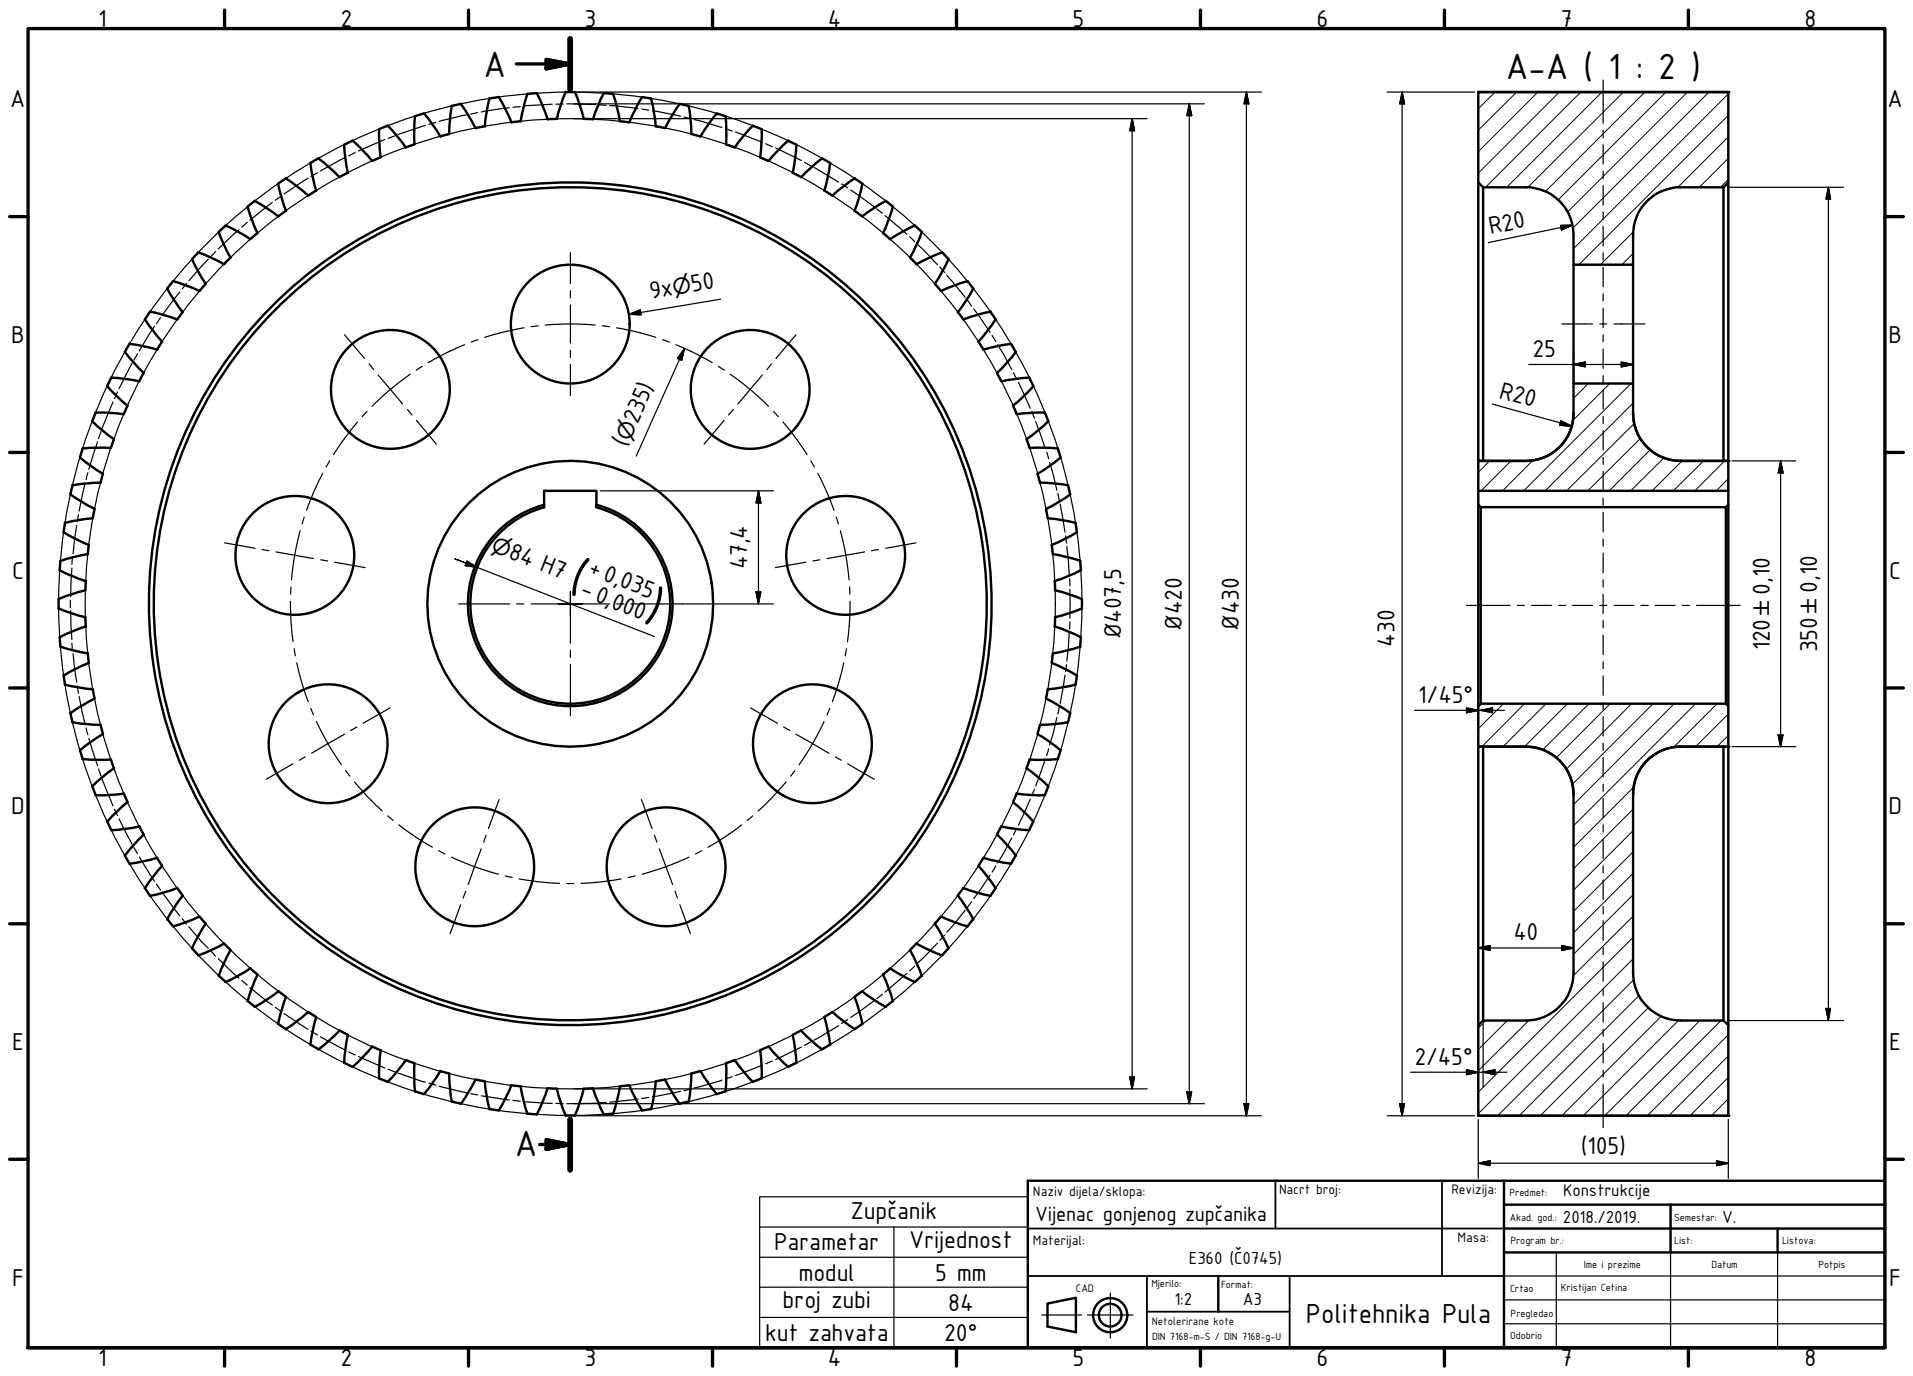
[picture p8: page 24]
F CAD; Netolerirane kote; DIN 7168-m-S / DIN 7168-g-U; Zupúanik; Parametar; Vrijednost; modul; broj zubi; kut zahvata

Naziv dijela/sklopa: Vijenac gonjenog zupúanika | Nacrt broj: | Revizija: | Konstrukcije Predmet:

2018./2019. Akad. god.: | V. Semestar:

Materijal: E360 (ù0745) | Masa: | Program br.: | List: | Listova:

Ime i prezime | Datum | Potpis

Mjerilo: 1:2 | Format: A3 | Politehnika Pula | Crtao | Kristijan Cetina

Pregledao

Odobrio

A-A ( 1 : 1 )
A

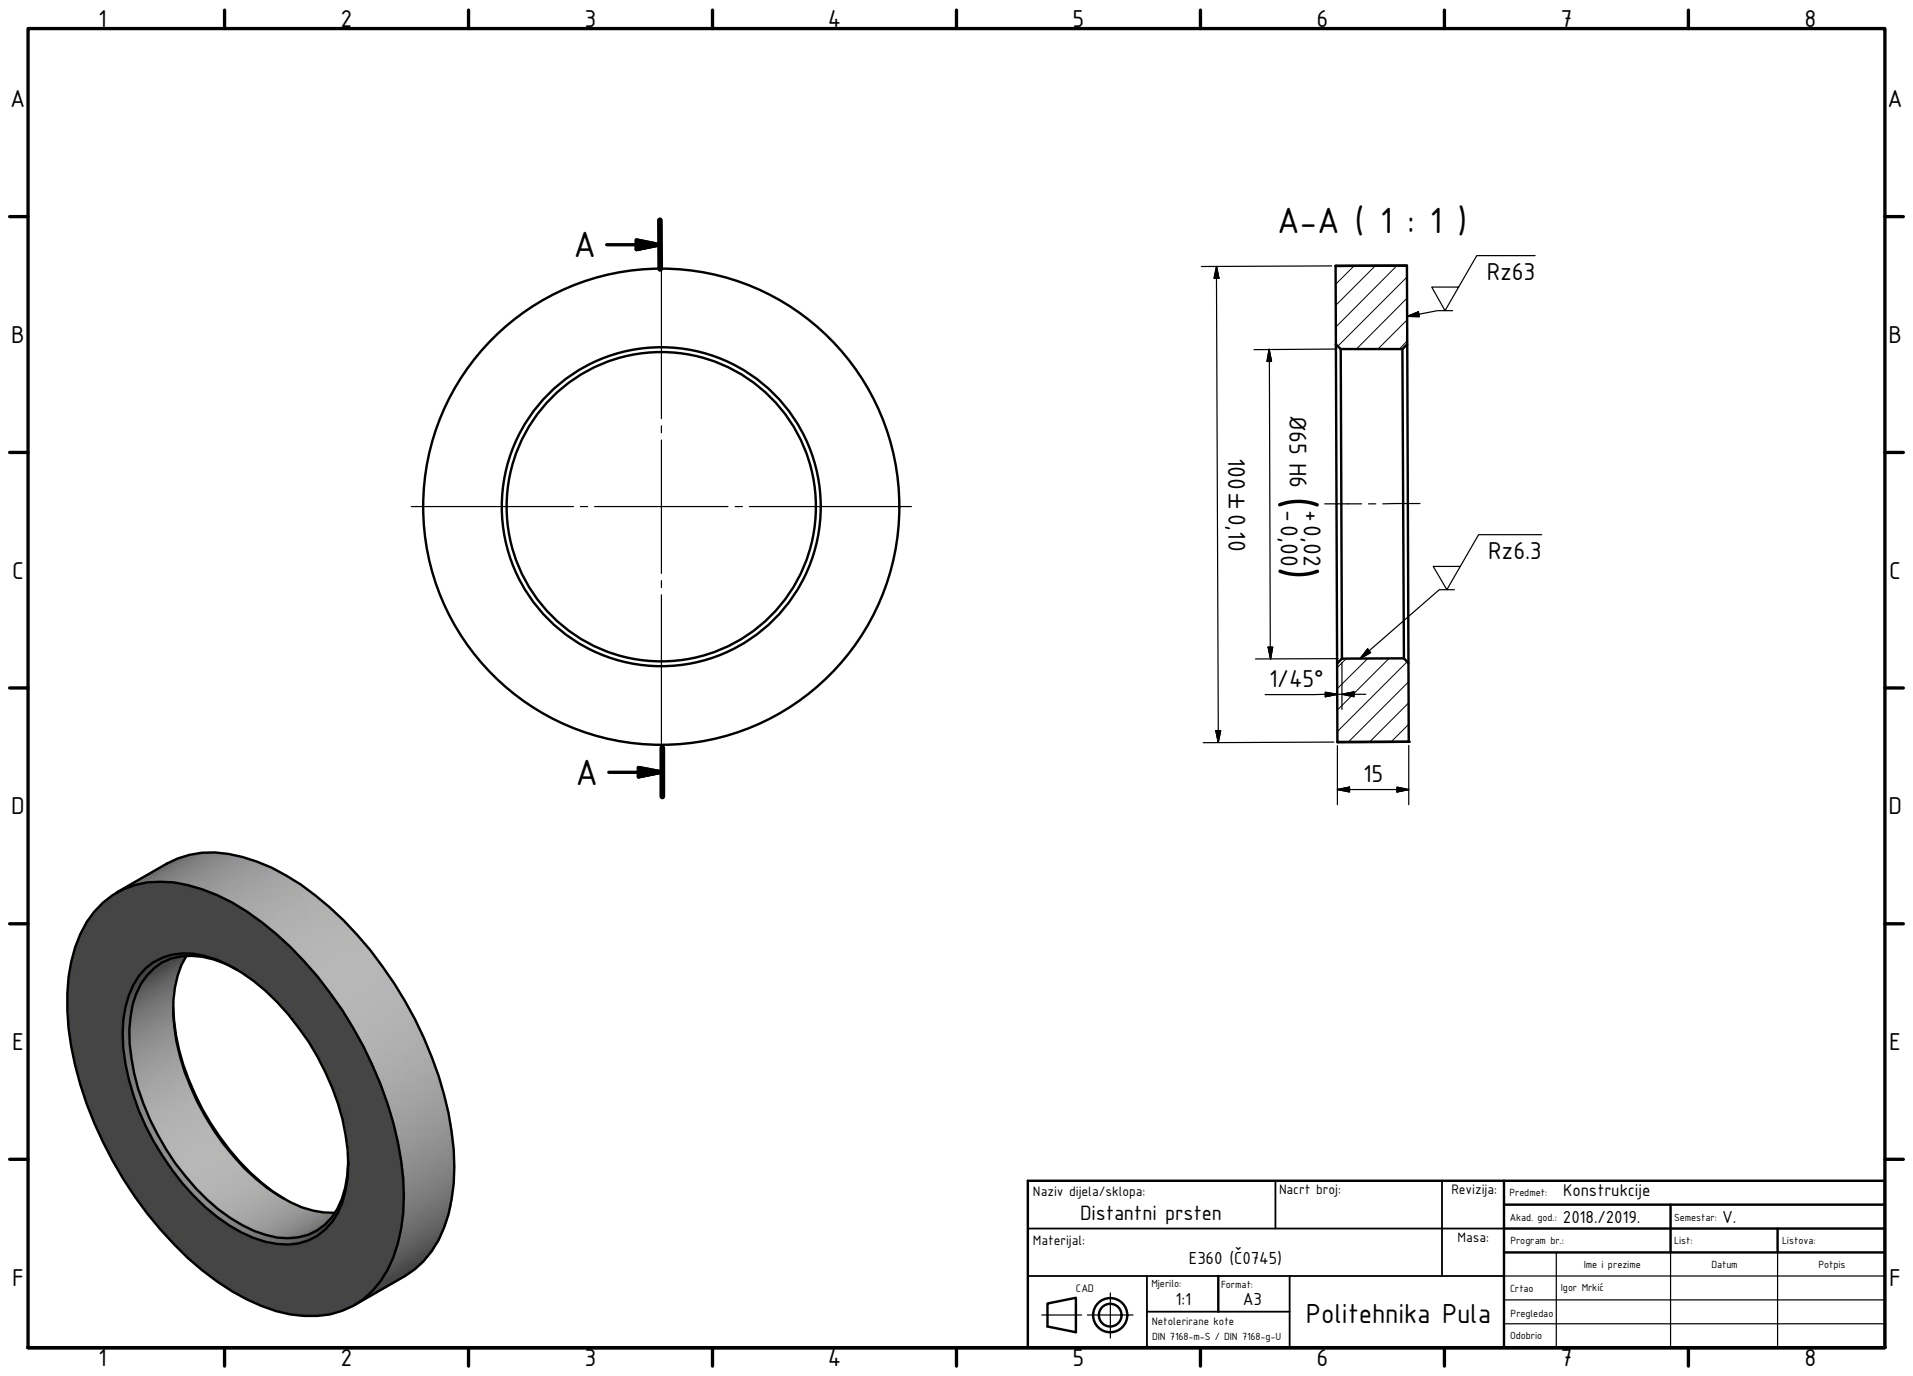
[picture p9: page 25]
F CAD; Netolerirane kote; DIN 7168-m-S / DIN 7168-g-U

Naziv dijela/sklopa: Distantni prsten | Nacrt broj: | Revizija: | Konstrukcije Predmet:

2018./2019. Akad. god.: | V. Semestar:

Materijal: E360 (ù0745) | Masa: | Program br.: | List: | Listova:

Ime i prezime | Datum | Potpis

Mjerilo: 1:1 | Format: A3 | Politehnika Pula | Crtao | Igor Mrkiô

Pregledao

Odobrio

1

2

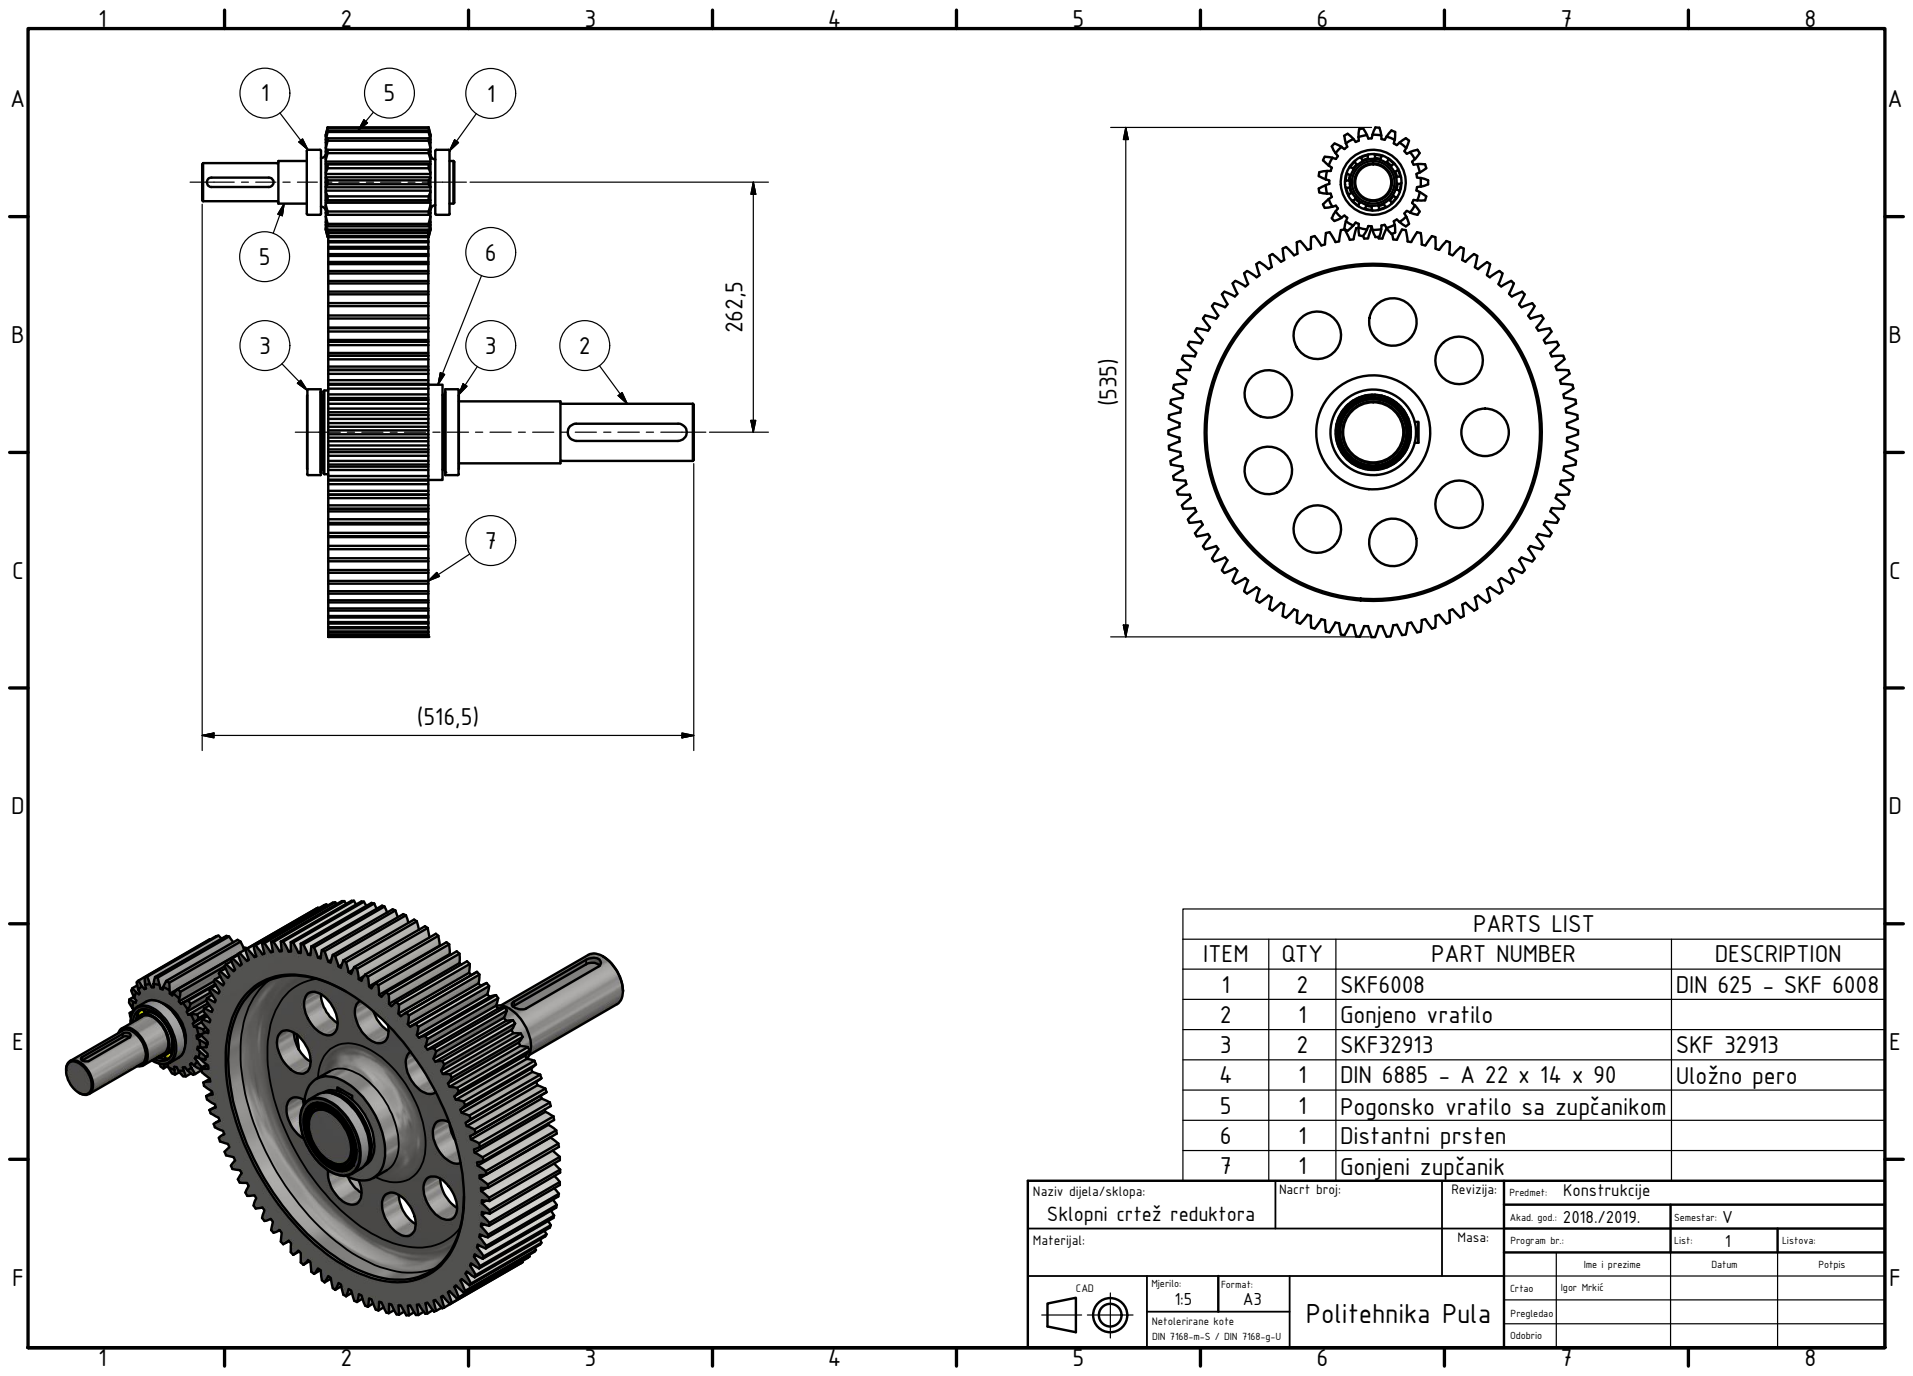
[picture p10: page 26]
PARTS LIST; ITEM; QTY; PART NUMBER; DESCRIPTION; F CAD; Netolerirane kote; DIN 7168-m-S / DIN 7168-g-U

1 | 2 | SKF6008 | DIN 625 - SKF 6008
2 | 1 | Gonjeno vratilo
3 | 2 | SKF32913 | SKF 32913
4 | 1 | DIN 6885 - A 22 x 14 x 90 | Ulono pero
5 | 1 | Pogonsko vratilo sa zupúanikom
6 | 1 | Distantni prsten
7 | 1 | Gonjeni zupúanik

Naziv dijela/sklopa: Sklopni crte reduktora | Nacrt broj: | Revizija: | Konstrukcije Predmet:

2018./2019. Akad. god.: | V Semestar:

Materijal: | Masa: | Program br.: | List: 1 | Listova:

Ime i prezime | Datum | Potpis

Mjerilo: 1:5 | Format: A3 | Politehnika Pula | Crtao | Igor Mrkiô

Pregledao

Odobrio

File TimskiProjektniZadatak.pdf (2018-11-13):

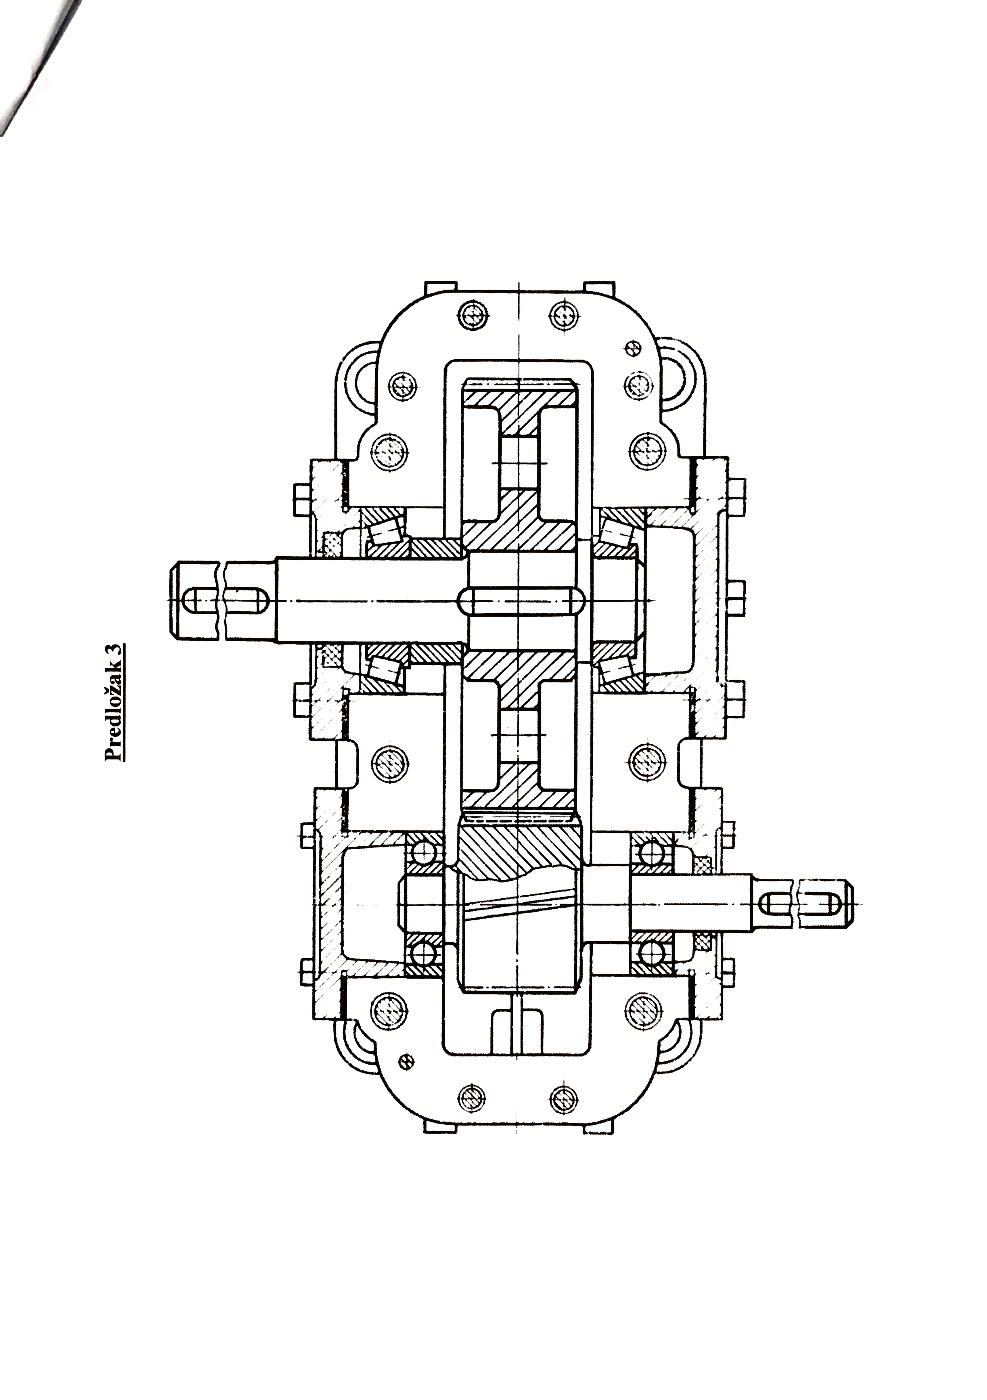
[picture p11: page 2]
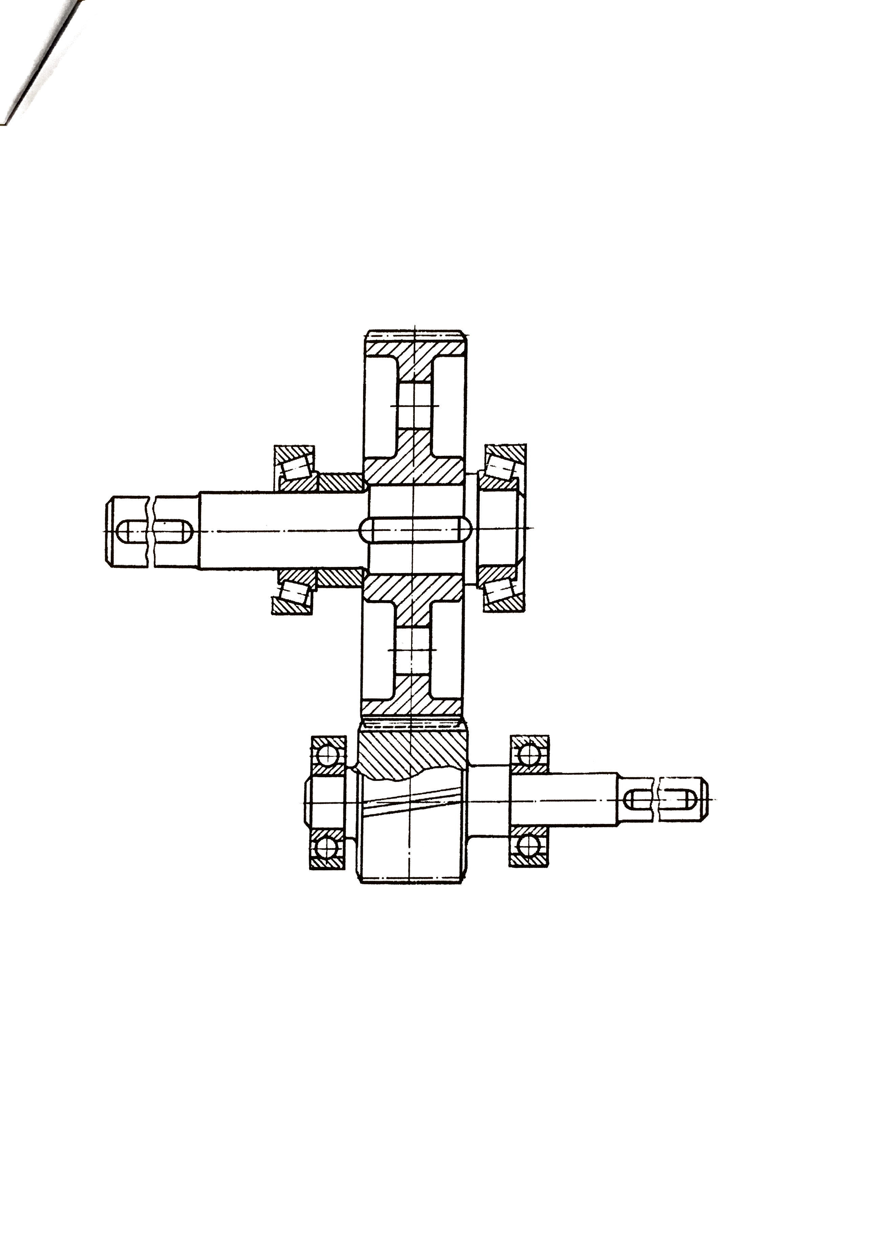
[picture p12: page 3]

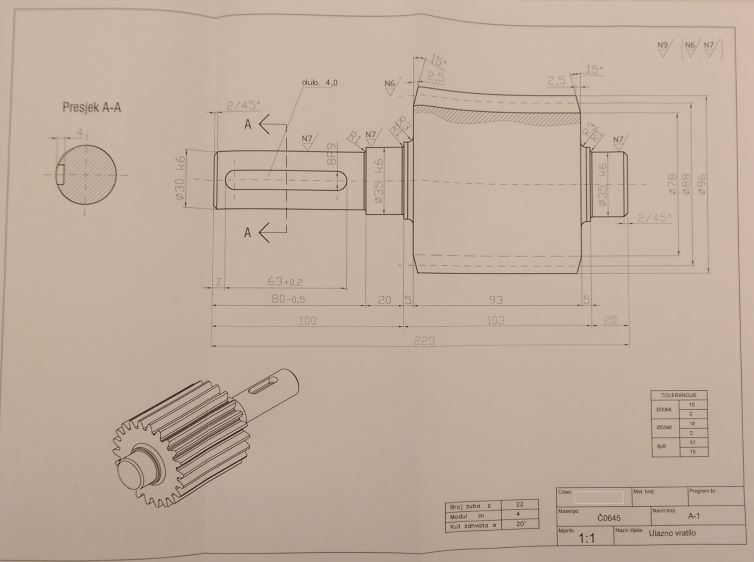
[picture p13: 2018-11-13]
PotrebniMaterijali/4-Vježbe - Izrada nacrta - Pogonsko vratilo - Primjer.JPG

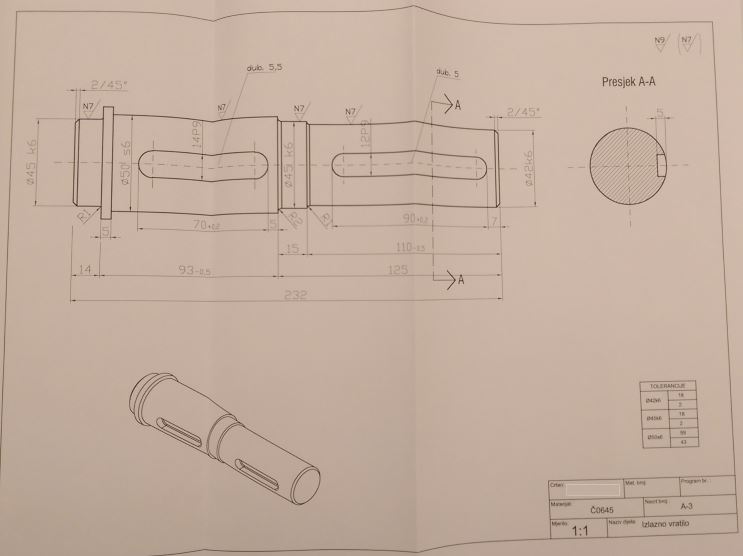
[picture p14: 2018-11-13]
PotrebniMaterijali/4-Vježbe - Izrada nacrta - Gonjeno vratilo - Primjer.JPG

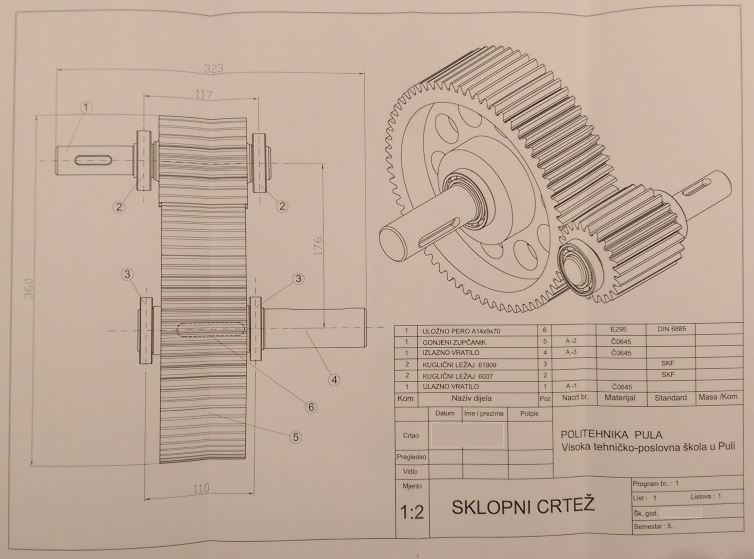
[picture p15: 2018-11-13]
PotrebniMaterijali/4-Vježbe - Izrada nacrta - Sklopni crtez - Primjer.JPG

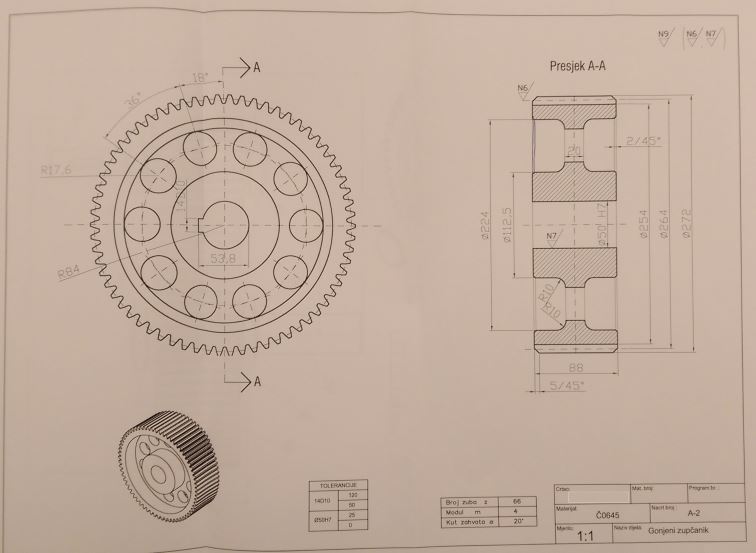
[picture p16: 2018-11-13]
PotrebniMaterijali/4-Vježbe - Izrada nacrta - Gonjeni zupčanik - Primjer.JPG

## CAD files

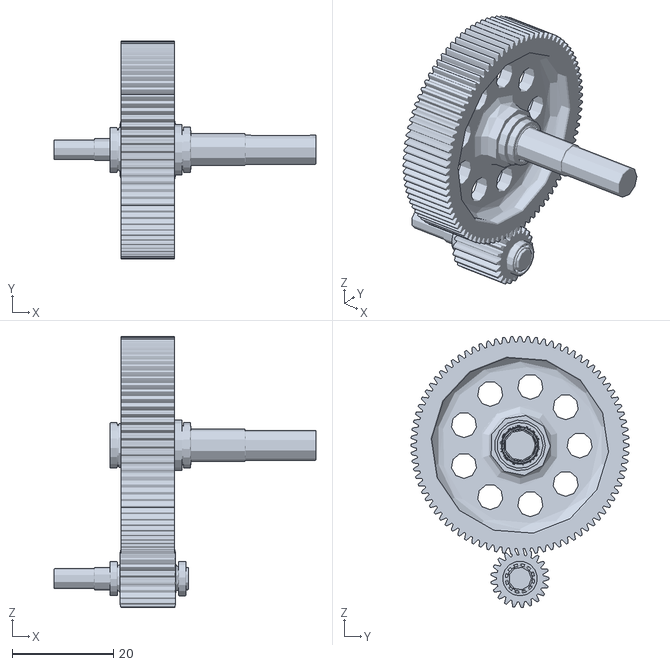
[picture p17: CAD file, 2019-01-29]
OutputDrawings/SklopReduktora.stl
51.7 x 43.0 x 53.5

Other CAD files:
OutputDrawings/DistantniPrsten.idw
OutputDrawings/DistantniPrsten.ipt
OutputDrawings/GonjeniZupcanikLight.idw
OutputDrawings/GonjeniZupcanik_olaksani.ipt
OutputDrawings/GonjenoVratilo.idw
OutputDrawings/GonjenoVratilo.ipt
OutputDrawings/PogonskoVratilo.idw
OutputDrawings/PogonskoVratiloSaZupcanikom.ipt
OutputDrawings/SklopReduktora.iam
OutputDrawings/SklopniNacrtReduktora.idw
datasheetsModels/32913.iam
datasheetsModels/32913_cage.ipt
datasheetsModels/32913_ir.ipt
datasheetsModels/32913_or.ipt
datasheetsModels/32913_roller.ipt
datasheetsModels/6008.iam
datasheetsModels/6008_PART1.ipt
datasheetsModels/6008_PART2.ipt
datasheetsModels/6008_PART3.ipt
datasheetsModels/6008_PART4.ipt
datasheetsModels/DIN 6885 - A 22 x 14 x 90.ipt

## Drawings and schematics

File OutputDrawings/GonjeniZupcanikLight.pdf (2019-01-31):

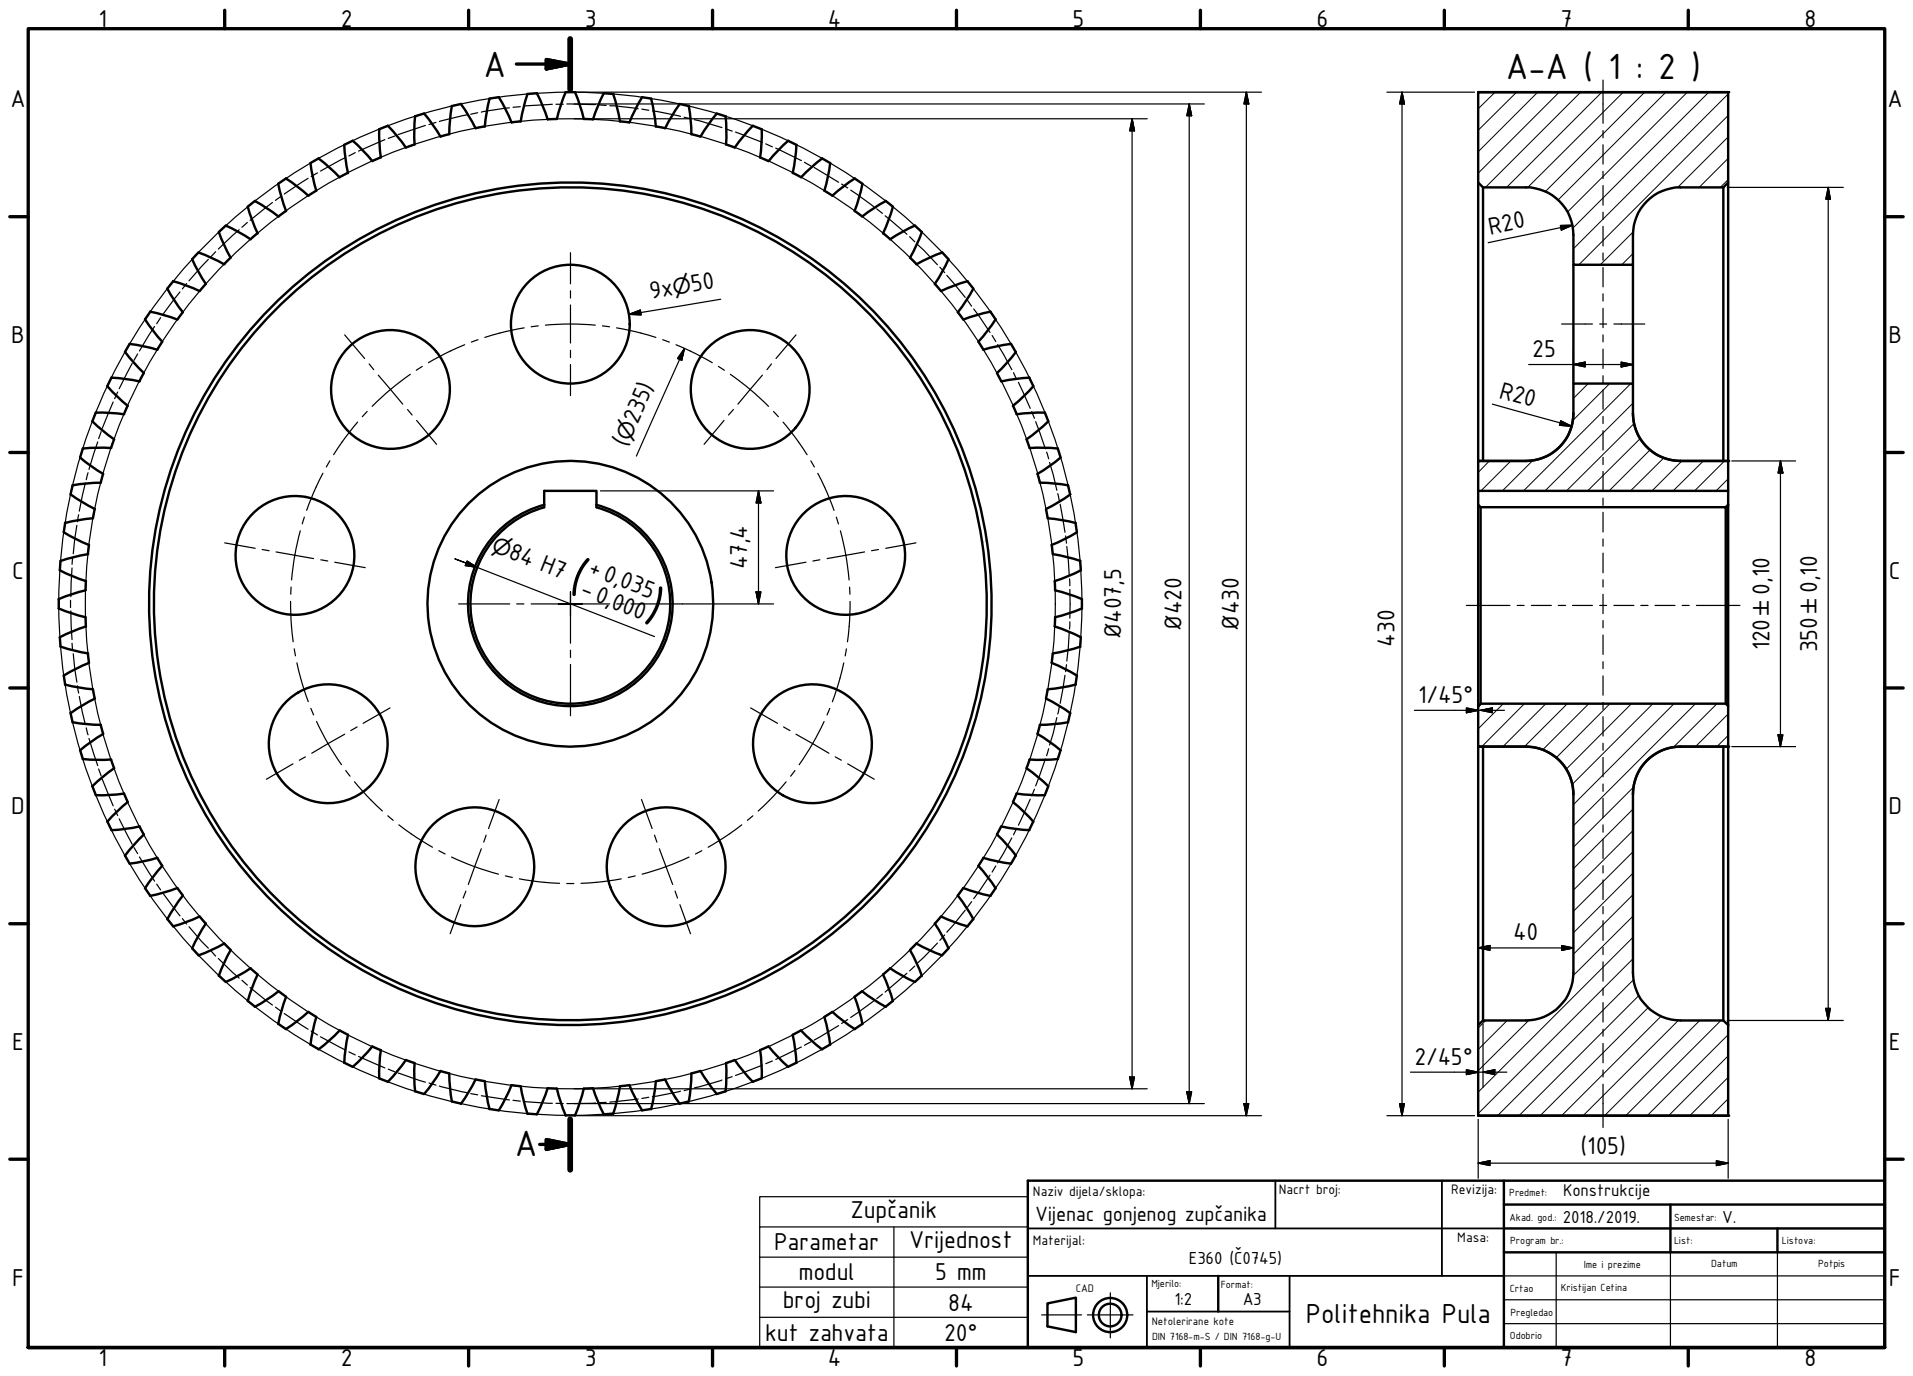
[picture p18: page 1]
F CAD; Netolerirane kote; DIN 7168-m-S / DIN 7168-g-U

Naziv dijela/sklopa: Vijenac gonjenog zupúanika | Nacrt broj: | Revizija: | Konstrukcije Predmet:

2018./2019. Akad. god.: | V. Semestar:

Parametar | Vrijednost | Materijal: E360 (ù0745) | Masa: | Program br.: | List: | Listova:
modul | 5 mm
broj zubi | 84
kut zahvata | 20n

Ime i prezime | Datum | Potpis

Mjerilo: 1:2 | Format: A3 | Politehnika Pula | Crtao | Kristijan Cetina

Pregledao

Odobrio

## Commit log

2018-11-17 RucniProracun, modeli
    Dodan ručni proračun i 3D modeli odabranih ležajeva
    [32912.iam, 32912_cage.ipt, 32912_ir.ipt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]
2018-11-17 Pogonsko vratilo 3dmodel
    [PogonskoVratilo.0002.ipt, PogonskoVratilo.ipt]
2018-11-17 novi ležaj; .lck to ignore
    [32913.iam, 32913_cage.ipt, 32913_ir.ipt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]
2018-11-17 nacrti vratila
    [GonjenoVratilo.idw, PogonskoVratilo.idw]
2018-11-17 removed OldVersions
    [GonjenoVratilo.0002.ipt, PogonskoVratilo.0002.ipt]
2018-11-17 update sklopa
    [GonjenoVratilo.ipt, SklopReduktora.iam]
2018-11-19 update plan rada
    [PogonskoVratilo.ipt]
2018-11-22 update rukavca ležajeva pogonskog vratila
    [PogonskoVratilo.idw, PogonskoVratilo.ipt, SklopReduktora.iam]
2018-11-24 Razmak osi zuba a, elaborat u toku
    [SklopReduktora.iam]
2018-11-24 Elaborat u toku, removed non used model
    [32912.iam, 32912_cage.ipt, 32912_ir.ipt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]
2018-11-24 rukavac ležaja gonjenog vratila
    [32913.iam, GonjenoVratilo.idw, GonjenoVratilo.ipt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]
2018-11-30 Promjena faktora sigurnosti pri preliminarnom proračunu pogonskog vratila 12 -> 11 da odgovara gonjenom
    [PogonskoVratilo.idw, PogonskoVratilo.ipt]
2018-12-09 ulozno pero na zupcaniku gonenog vratila
    [GonjenoVratilo.idw, GonjenoVratilo.ipt]
2018-12-09 ispravak uloznog pera zupcanika zonjenog vratila
    [GonjenoVratilo.idw, GonjenoVratilo.ipt]
2018-12-22 Create DIN 6885 - A 22 x 14 x 90.ipt
    [DIN 6885 - A 22 x 14 x 90.ipt]
2018-12-22 Složen sklop
    [GonjeniZupcanik.ipt, GonjenoVratilo.idw, GonjenoVratilo.ipt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]
2018-12-23 ispravljeno ulozno pero na gonjenom vratilu
    Prepravljeno da se koristi uložno pero (za spajanje gonjenog stroja) standardnih dimenzija (100mm -> 125mm).
    [GonjenoVratilo.idw, GonjenoVratilo.ipt, SklopReduktora.iam]
2018-12-25 ispravljena dimenzija utora za ulozno pero gonjenog vratila - spoj vijenca zupcanika
    [GonjenoVratilo.idw, GonjenoVratilo.ipt, SklopReduktora.iam]
2018-12-25 Dodan nacrt (nedovrseni) gonjenog zupcanika
    [GonjeniZupcanik.idw]
2019-01-12 Dodan distantni prsten
    [DistantniPrsten.idw, DistantniPrsten.ipt, GonjenoVratilo.idw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]
2019-01-16 zakrivljenosti na gonjenom vratilu
    [DistantniPrsten.idw, DistantniPrsten.ipt, GonjenoVratilo.idw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]
2019-01-19 Dodan sklopni nacrt reduktora
    [DistantniPrsten.idw, SklopReduktora.iam, SklopniNacrtReduktora.idw]
2019-01-20 detalji nacrta
    [DistantniPrsten.idw, GonjeniZupcanik.idw, GonjenoVratilo.idw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]
2019-01-20 Skošenje pogonskog zupčanika
    [DistantniPrsten.idw, PogonskoVratilo.idw, PogonskoVratiloSaZupcanikom.ipt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]
2019-01-21 update materijal izrade
    [32913.iam, 6008.iam, DIN 6885 - A 22 x 14 x 90.ipt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]
2019-01-23 Olaksani gonjeni zupčanik, nacrti
    [GonjeniZupcanikLight.idw, GonjeniZupcanik_olaksani.ipt, GonjenoVratilo.idw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]
2019-01-24 update nacrta
    [GonjeniZupcanikLight.idw, GonjeniZupcanik_olaksani.ipt, PogonskoVratiloSaZupcanikom.ipt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]
2019-01-24 update nacrta gonjenog vratila
    [GonjenoVratilo.idw]
2019-01-25 Update README.md
    dodana slika analize stresa solo per la bella figura
2019-01-26 Završna verzija
    [DistantniPrsten.idw, GonjeniZupcanikLight.idw, GonjenoVratilo.idw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]
2019-01-26 Refinirana analiza
    [SklopReduktora.iam]
2019-01-29 Create SklopReduktora.stl
    Priprema .stl za 3d print
    [SklopReduktora.stl]
2019-01-31 removed excess drawings
    [GonjeniZupcanik.idw, GonjeniZupcanik.ipt]
2019-01-31 ispravljene ukazane greške na nacrtima
    [GonjeniZupcanikLight.idw, GonjenoVratilo.idw, PogonskoVratilo.idw]
